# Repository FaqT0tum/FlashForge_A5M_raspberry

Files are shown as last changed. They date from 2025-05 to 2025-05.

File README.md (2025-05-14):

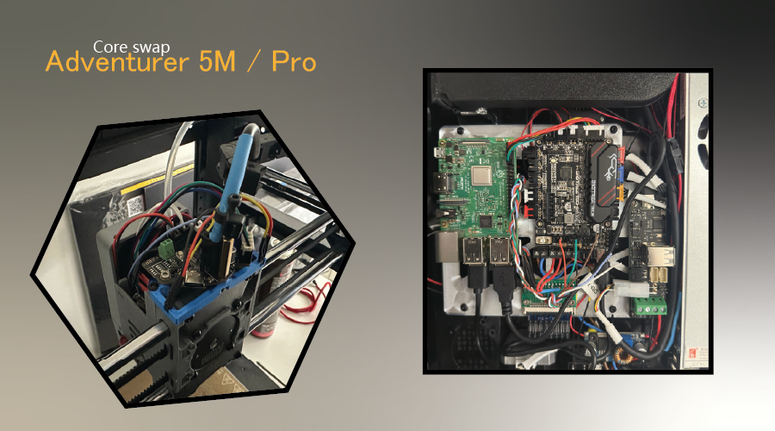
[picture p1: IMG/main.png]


The project will aim to completely replace all the electronics, leaving the original PSU, BED and head components.
 
 Some components will be mandatory and others can be replaced with what you prefer based on your needs.

## Components:

-  [FPC Brackout 30p 1mm](https://s.click.aliexpress.com/e/_oCeUnud) Bed wiring
-  [FPC Brackout 40p 0.5mm](https://s.click.aliexpress.com/e/_oB8gCY1) LCD Wiring (Coming soon)
-  [Hall effect A3144E](https://s.click.aliexpress.com/e/_oCG6PCH) Endstop X/Y
-  [Biqu EBB36 without MAX31865 v1.2](https://s.click.aliexpress.com/e/_oo8DyPB) Head Board
-  [Biqu U2C v2.1](https://s.click.aliexpress.com/e/_oo8DyPB) CAN transceiver
-  [Biqu SKR Pico v1](https://s.click.aliexpress.com/e/_omrGoLB) Main MCU
-  [Raspberry Pi Model B (at lest 1Gb)](https://s.click.aliexpress.com/e/_olvGKEN) SBC CPU Core
-  [Micro SD 64gb v30](https://s.click.aliexpress.com/e/_ooCZ32p) OS Memory (32gb v30 is also fine)
-  [Self-tapping M2.6 14mm](https://s.click.aliexpress.com/e/_oBh7XHr) Fixing screws
-  [Micro Molex 2x2](https://s.click.aliexpress.com/e/_olB1evL) to adapt EBB36
-  [Cable 22awg](https://s.click.aliexpress.com/e/_oD4gPCd) any extensions
-  [JST Crimping tool](https://s.click.aliexpress.com/e/_op3xPZP)
-  PETG 50g for adapters board

## Softwares
- [Raspberry PI Imager](https://www.raspberrypi.com/software/) Make File system
- [STM32 CubeProg](https://www.st.com/en/development-tools/stm32cubeprog.html) Flashing U2C/EBB36
- [Bitvise](https://bitvise.com/download-area) SSH for communicate with the Raspberry

## Configuration

- [Install Klipper (Kiauh)](https://github.com/dw-0/kiauh)
- [CanBus](https://github.com/FaqT0tum/FlashForge_A5M_raspberry/blob/main/CanBus/canbus.md)

## Electronics

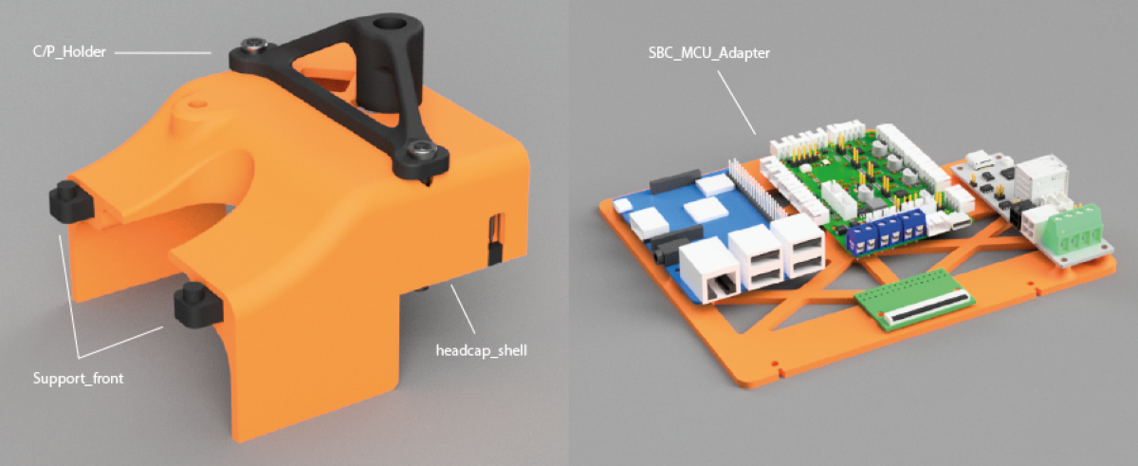
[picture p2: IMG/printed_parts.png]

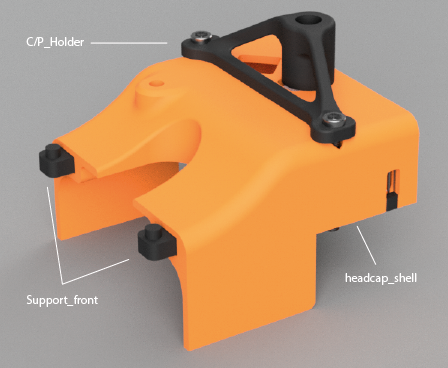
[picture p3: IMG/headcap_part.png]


<details>
<summary>Fan blower</summary>

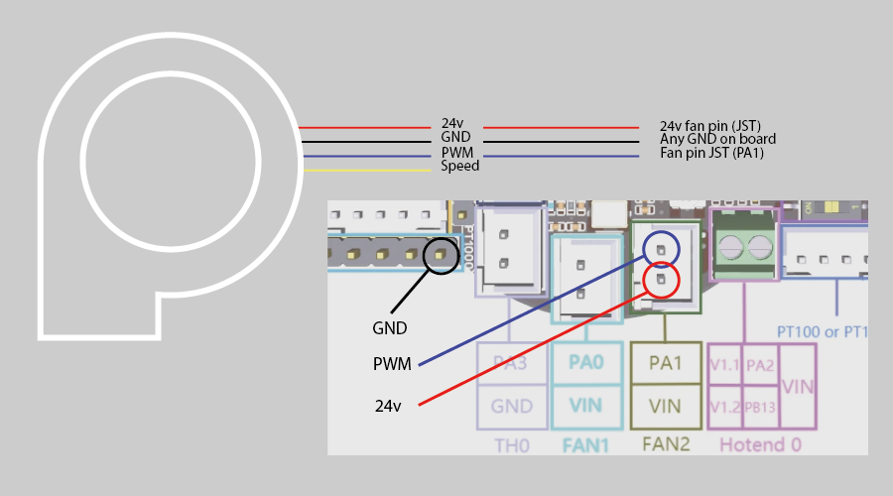
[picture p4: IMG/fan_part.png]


### Note: for the remaining FANS, the poles in the JST connectors must be reversed to adapt them to the SKR Pico

</details>

<details>
<summary>Filament runout</summary>

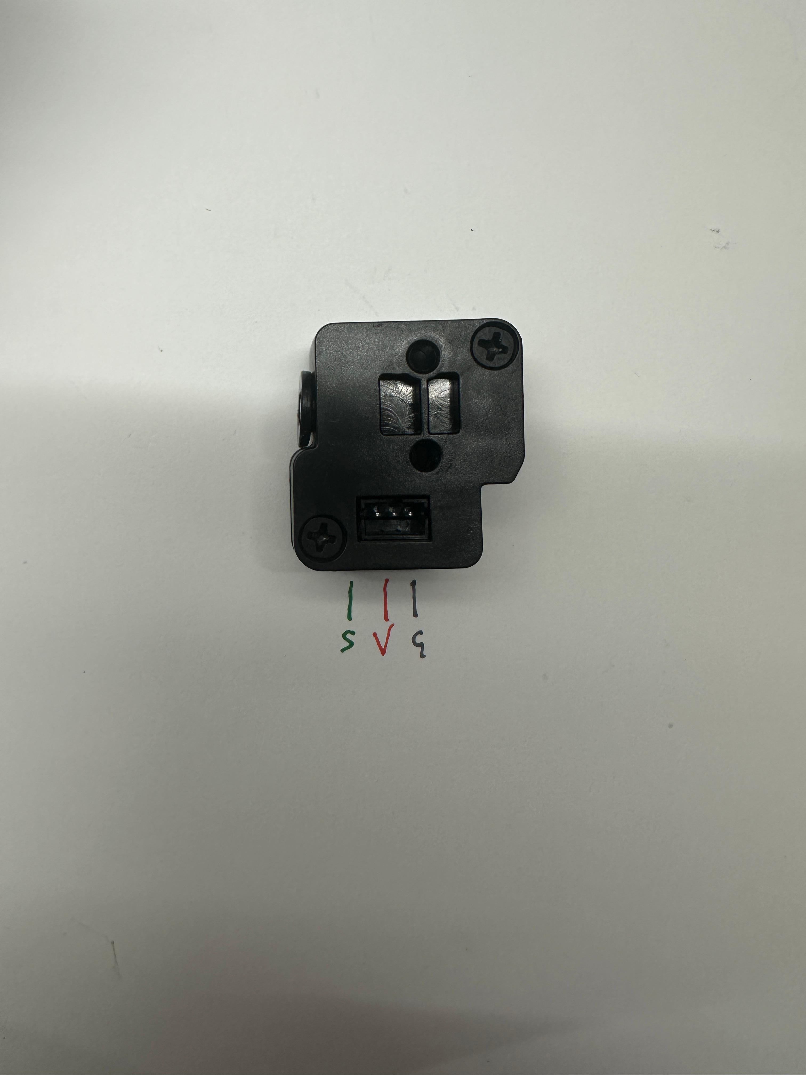
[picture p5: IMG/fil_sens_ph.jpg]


| Runout  | MCU |  
|:---:| :---:  |
| S | Signal | 
| V | 5V | 
| G | Ground | 

### Example

```bash
    [filament_switch_sensor runout_sensor]
    pause_on_runout: False
    switch_pin: !gpio3
    event_delay: 1.0
    runout_gcode:
        _FILAMENT_RUNOUT_EVENT
```

</details>

<details>
<summary>Heat Bed / Load Cell</summary>

### Connection diagram to reuse the original FFC and adapt it to the new MCU with a FPC Breakout 30p (1mm)

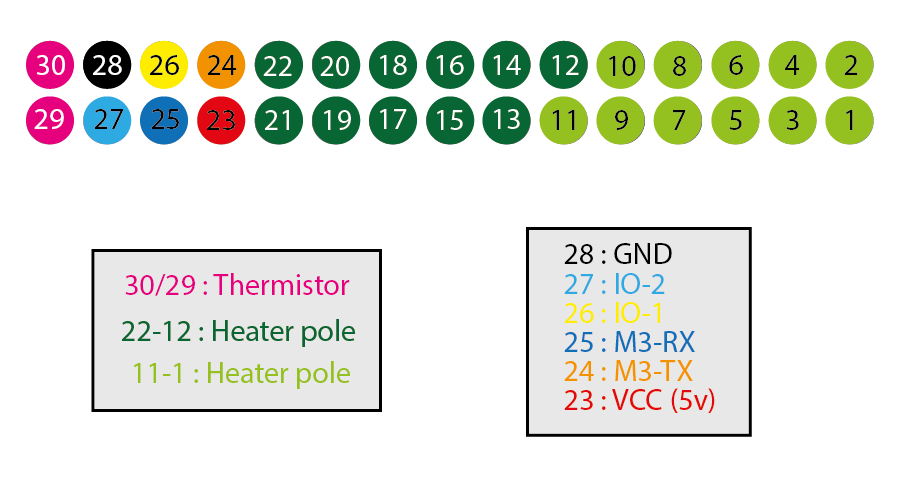
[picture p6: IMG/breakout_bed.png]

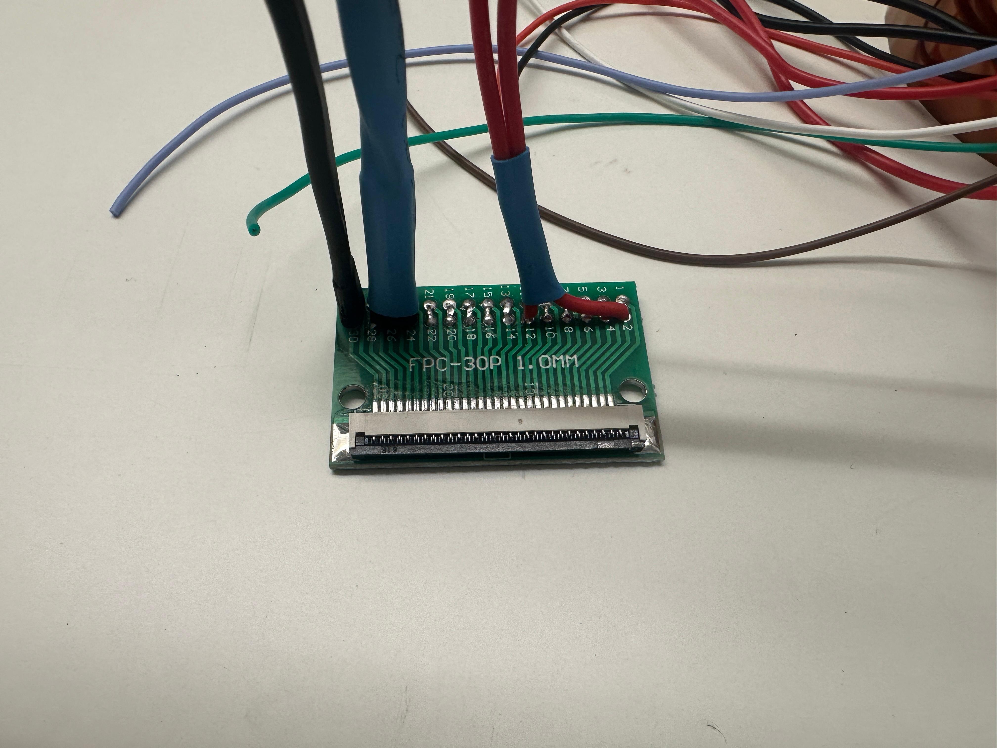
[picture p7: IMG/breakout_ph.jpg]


### Pins 23 to 28 are used for Load cell

### UPDATE: I was able to use the load cell system as a probe but without all the cell auto-calibration system without rebooting the board.
very simply, just connect the cables like this:

| FPC  | MCU |  
|:---:| :---:  |
| GND | GND | 
| VCC | 5V | 
| IO-1 | endstop pin | 

In my setup I connected everything to the JST x-stop of the SKR Pico using the reverse gpio4 pin (!)

```bash
    [probe]
    pin: !gpio4
    z_offset: -0.25
    speed: 2
    lift_speed: 5
    samples: 1
```

in the diagram below are shown the flashforge elettronics between Load_cell board --> FPC --> Main board. 
For future developments

| STC8G  | FPC | N32G455 | 
|:---:| :---:  | :---: |
| 1 | IO-2 | PB3 | 
| 3 | IO-1 | PB4 |  
| 5 | M3-TX  | PC12  | 
| 6 | M3-RX  | PD2 |  

</details>

<details>
<summary>Headtool board</summary>

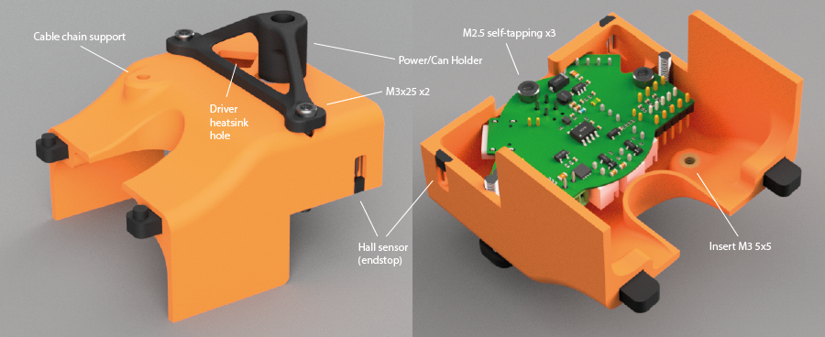
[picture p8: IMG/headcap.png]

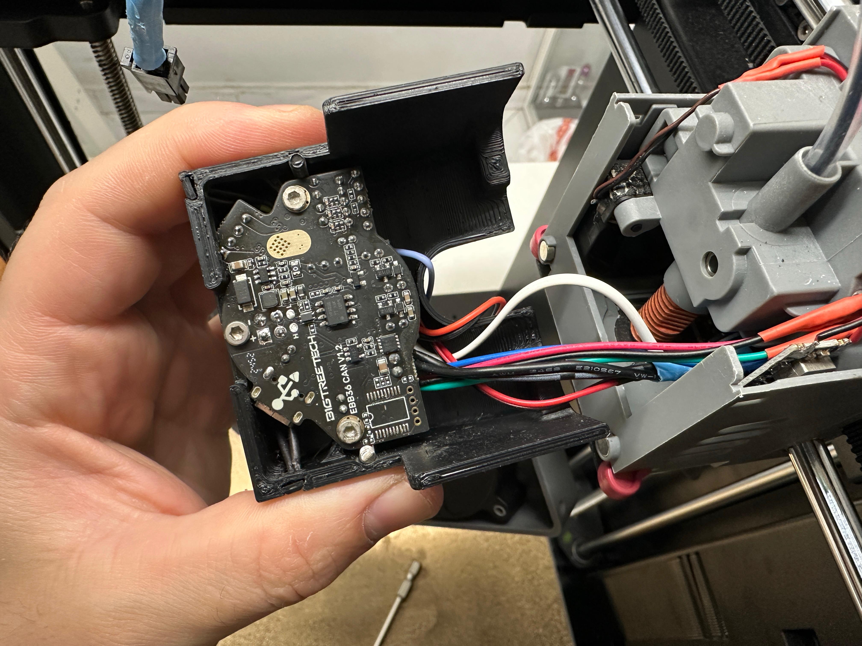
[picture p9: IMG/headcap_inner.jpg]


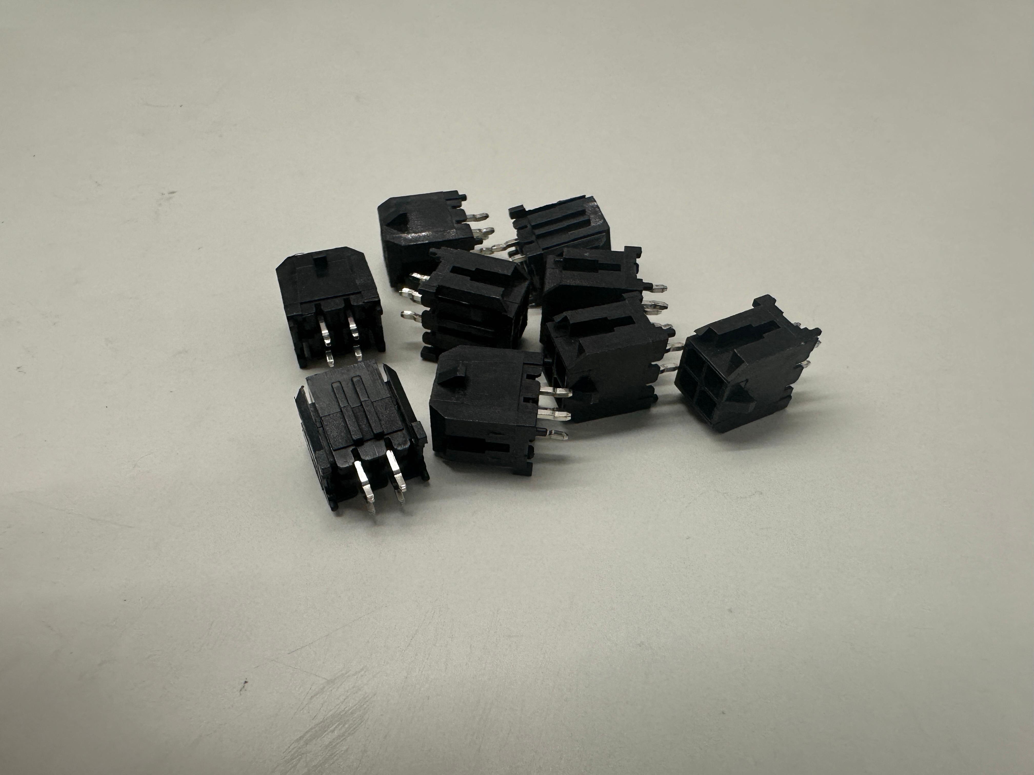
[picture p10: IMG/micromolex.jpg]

### For the assembly of the Had board requires a modification to the original Micro molex 2x2 90deg connector of the ebb36 with a straight one, Otherwise it will hit the back of the printer
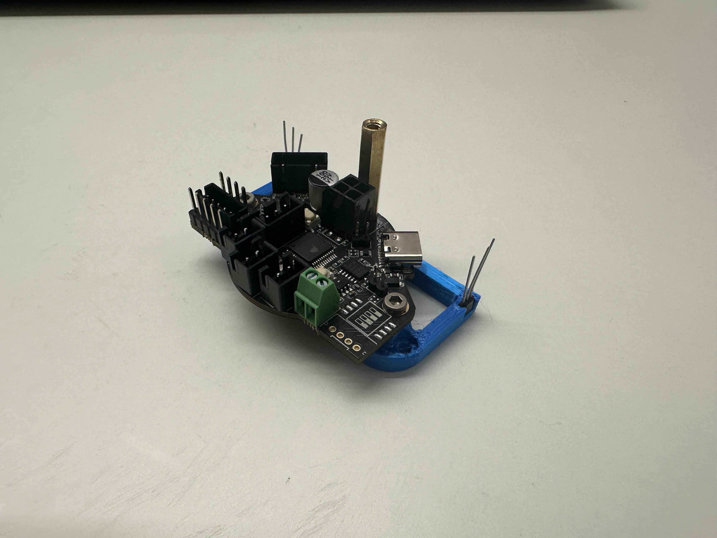
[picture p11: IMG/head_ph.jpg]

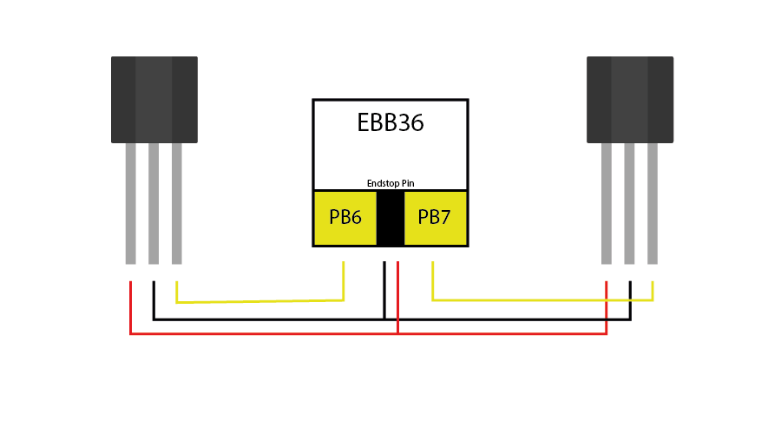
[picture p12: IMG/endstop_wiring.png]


</details>

### the above entries are expandable, click on the arrows

# Social

- [Instagram](https://www.instagram.com/faq_t0tum/)
- [YouTube](https://www.youtube.com/channel/UCHJ_528ZI0BcSU-QA8kIJlg)
- [PrusaPrinter](https://www.prusaprinters.org/social/218145-faqtotum/about)

# Buy me a coffee

This project is Free so if you have the pleasure of supporting my next works I will be grateful fot the coffee.  
[PayPal](https://www.paypal.me/MattiaRusso308?locale.x=it_IT)

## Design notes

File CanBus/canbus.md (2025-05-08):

# Configuration and installation of the Canbus U2C and EBB36 boards
The guide is based on Erik Zimmerman's, not because it is wrong, but to optimize it based on my experience and to minimize the problems I encountered.
The original guide can be found [here](https://github.com/EricZimmerman/VoronTools/blob/main/EBB_CAN.md) 

The components I used in this guide are:

1. Raspbery Pi 5
2. BTT U2C Version (2.1)
3. BTT EBB36 Version (1.2)
4. Some wire in the 22awg range
5. USB cables (I recommend that you make sure that the Type-C cable is not only power but also DATA)
6. A little patience :)

Before proceeding with the configuration of the various components, 
I recommend doing everything outside of the printer to make the various steps that will come easier for you.

# Raspberry setup

First we need to access the raspberry from the PC via SSH, to do this we will use Bitvise, entering the IP address that was assigned to the raspberry by the Router, in port we enter (22), username and password chosen during the creation of Raspberry OS.
If no user or password has been chosen you can use the default ones of the raspberry (User: pi / Password: raspberry). It is recommended to change at least the password at the first boot

1. Use mkdir to create a new folder with the command `sudo mkdir /etc/network/interfaces.d`
2. Use nano to create a new file with the command `sudo nano /etc/network/interfaces.d/can0`
3. Add the following code
    ```bash
    allow-hotplug can0
    iface can0 can static
     bitrate 1000000
     up ifconfig $IFACE txqueuelen 1024
     pre-up ip link set can0 type can bitrate 1000000
     pre-up ip link set can0 txqueuelen 1024
     ```

4. Use nano to create a new file with the command `sudo nano /etc/systemd/network/10-can.link`
5. Add the following code then save and exit nano
    ```bash
    [Match]
    Type=can
    
    [Link]
    TransmitQueueLength=1024
    ```

6. Use nano to create a new file with the command `sudo nano /etc/systemd/network/25-can.network`
7. Add the following code then save and exit nano
    ```bash
    [Match]
    Name=can*
    
    [CAN]
    BitRate=1M
    ```

8. Now you need to add a line to bottom in crontab for enable canbus at startup, with the command `sudo crontab -e`
9. Add the following code then save and exit nano. If asked for the editor type, select (1 - nano)
    ```bash

    @reboot sudo ip link set up can0 type can bitrate 1000000 &

    ```
10. Reboot the pi with `sudo reboot`

# U2C Flashing

Now to make sure that U2C has the right firmware we need to flash it with the correct version available [here](https://github.com/FaqT0tum/FlashForge_A5M_raspberry/blob/main/CanBus/G0B1_U2C_V2.zip)

1. The steps to flash this firmware are (taken from above link):
    - Download the STM32 CubePROG [here](https://www.st.com/en/development-tools/stm32cubeprog.html) 
    - Unzip the firmware file, previously downloaded
    - Press and hold the boot button on the u2c and plug the usb cable on PC, then release the boot button.
    - Launch STM32 CubePROG
    - Press the blue button that says (UART) and change it to (USB), and connect
    - Press on the green download symbol on the left
    - Browse and select a G0B1_U2C_V2.bin
    - Press (Start Programming)
    - unplug and reconnect the U2C to the Raspberry
    - Success
3. ADD THE JUMPER for the 120 ohm resistor to the U2C and set the U2C aside
    
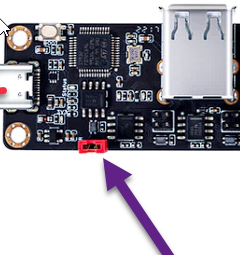
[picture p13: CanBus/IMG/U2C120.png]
    

# EBB36 Flashing

### Building Katapult (formerly known as CanBoot)

1. Clone the Katapult repository to your pi
    ```bash
    cd ~
    git clone https://github.com/Arksine/katapult
    ```

2. Run the following commands to bring up the menu to configure the firmware
    ```bash
    cd katapult
    make menuconfig
    ```
    
3. Starting from the top, make your firmware selections look exactly like the image below
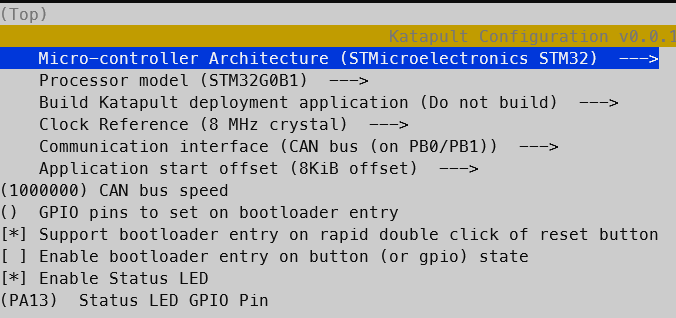
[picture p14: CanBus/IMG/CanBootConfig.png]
    

    NOTE: For Status LED GPIO Pin, be sure to enter **PA13**
    
4. Exit using `ESC` or `Q`, then confirm with yes (`Y`)
5. Build the firmware using the following commands:
    ```
    make clean
    make
    ```
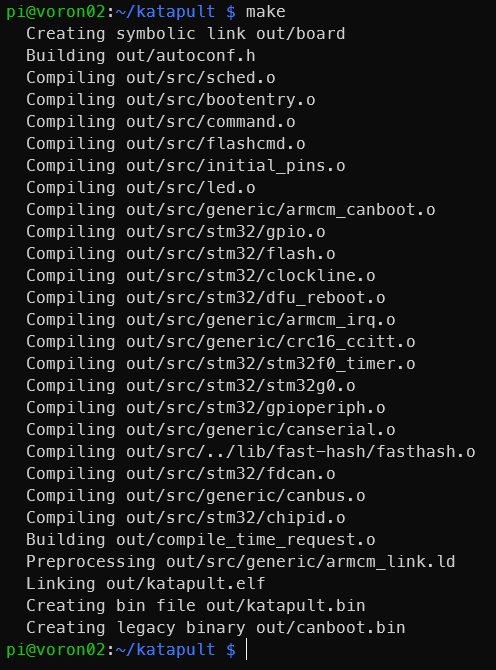
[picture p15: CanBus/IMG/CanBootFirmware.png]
    

### Flashing Katapult

1. Add a jumper as shown in the image below so the board can be powered via a USB connection
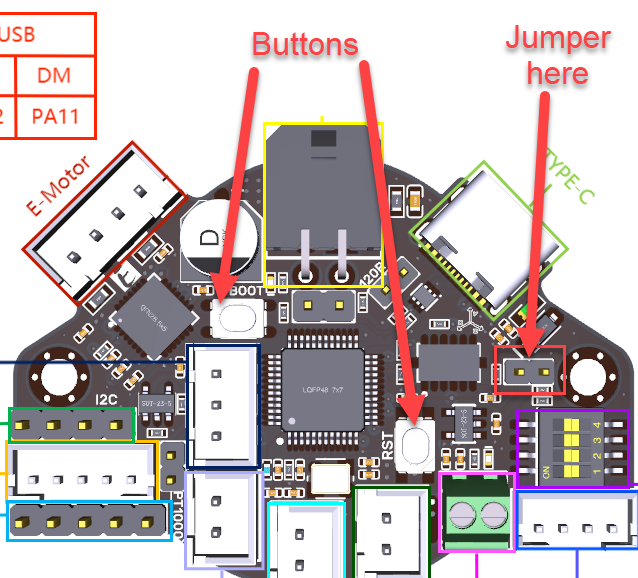
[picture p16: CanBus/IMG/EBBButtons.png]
    

2. Connect your device to your Pi via USB
3. Press and hold the `RESET` and `BOOT` buttons down (button locations shown in step 1)
    1. Release `RESET` button
    2. Release `BOOT` button
4. The device should now be in DFU mode. Verify this via the `lsusb` command, which should look something like this:
    ```
    Bus 001 Device 005: ID 0483:df11 STMicroelectronics STM Device in DFU Mode
    ```
5. Record the device ID (the part after `ID` above, but yours may be different)
6. Run the following command to erase and flash the EBB with Katapult (again, VERIFY your device ID. The ID is at the end of the command below):
    ```
    sudo dfu-util -a 0 -D ~/katapult/out/katapult.bin --dfuse-address 0x08000000:force:mass-erase:leave -d 0483:df11
    ```
7. The board will now be flashed. It will look similar to what is shown below. NOTE: If you see any mention of an error after the `File downloaded successfully` message, it can be ignored.

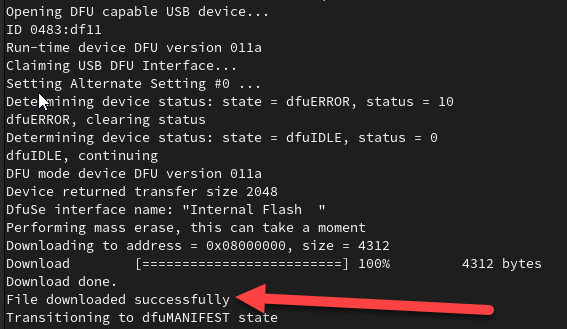
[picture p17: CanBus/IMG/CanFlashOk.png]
    
    
8. Unplug the board from USB and remove the USB jumper you installed for step 1
9. ADD THE JUMPER for the 120 ohm resistor to the EBB

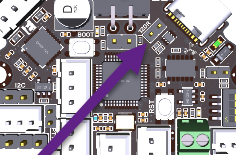
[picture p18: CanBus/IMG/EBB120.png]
    

### Verifying you see Katapult and flashing Klipper to the EBB

At this point, after checking twice that everything is connected correctly, power up the printer and SSH into the Pi.

1. Change directories into the klipper directory via `cd ~/klipper`
2. type `make menuconfig` and adjust things so it looks like the screenshot below

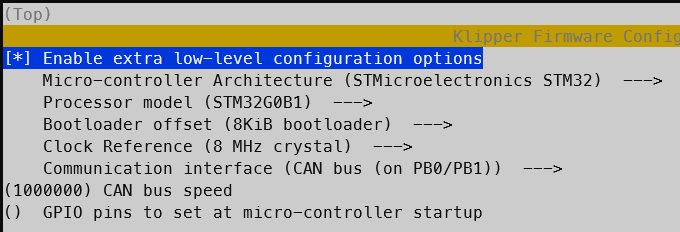
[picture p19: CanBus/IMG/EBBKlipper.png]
    

3. Exit, saving the changes, then build klipper by typing `make`
4. Find your UUID by running this command:
    ```bash
    sudo service klipper stop
    python3 ~/katapult/scripts/flashtool.py -i can0 -q
    ```
5. It should return something like:

    ```
    "Detected UUID: XXXXXXXXXX, Application: Katapult"
    ```

6. Record the UUID. This is YOUR uuid and will be used for the next step and in your cfg files.
7. Now its time to flash klipper via CAN! Run the following command, substituting your uuid:

   ```bash
   python3 ~/katapult/scripts/flashtool.py -i can0 -u b6d9de35f24f -f ~/klipper/out/klipper.bin
   ```
8. The EBB will be flashed and you should see a message about success, etc. Request for uuids again via:

   ```bash
    python3 ~/katapult/scripts/flashtool.py -i can0 -q
   ```

   but now, notice how it shows **Klipper** for the application! Yay!

9. Restart klipper via

   ```bash
   sudo service klipper start
   ```

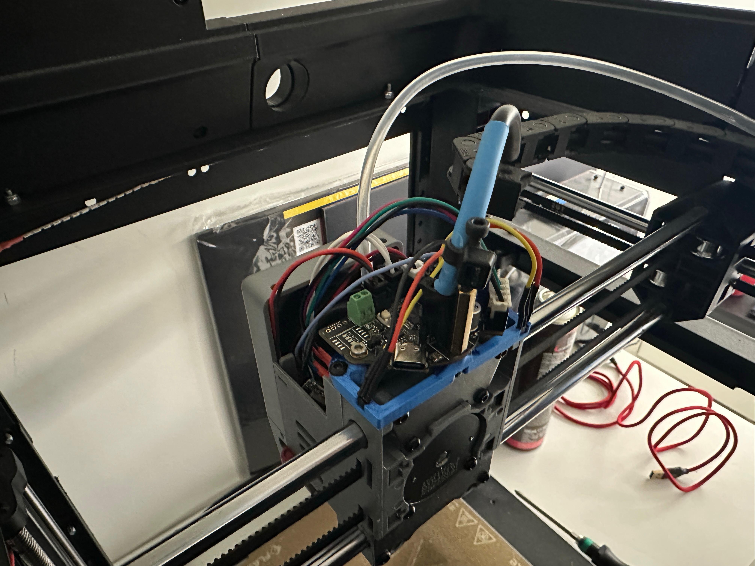
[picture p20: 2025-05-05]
IMG/head_pph.jpg

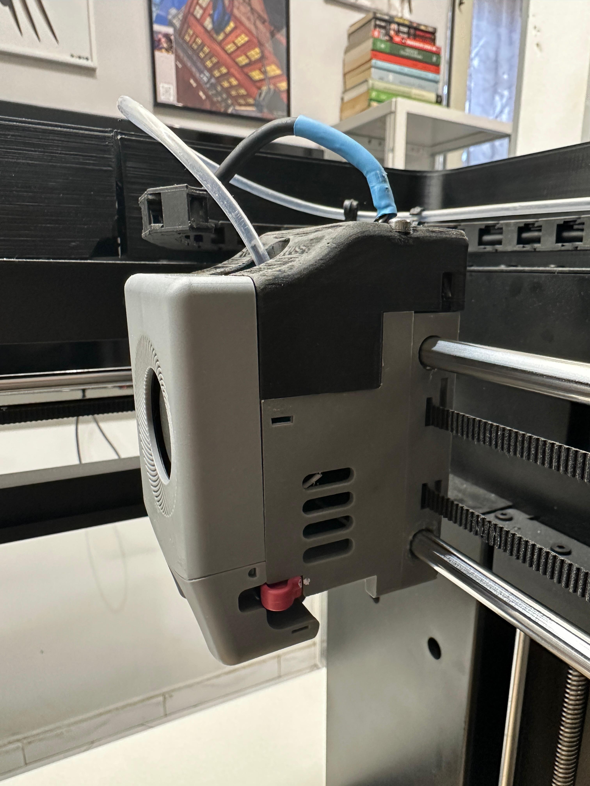
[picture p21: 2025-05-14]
IMG/headcap_side_ph.jpg

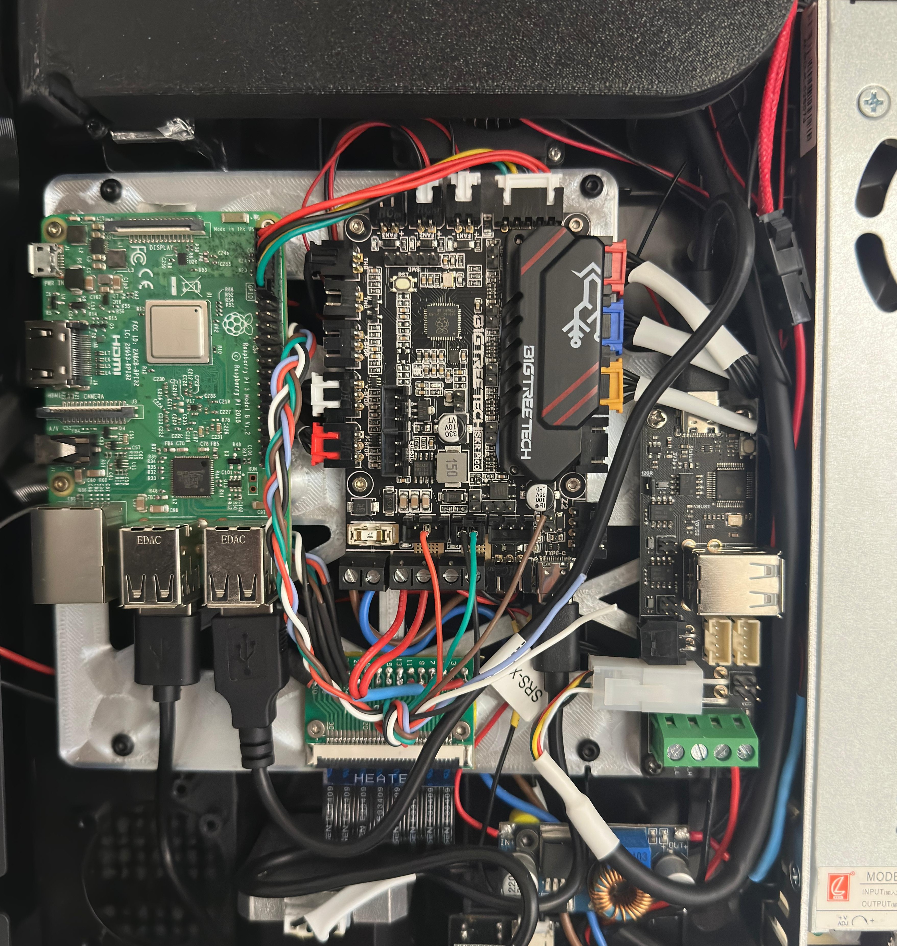
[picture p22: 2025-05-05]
IMG/main_ph.jpg

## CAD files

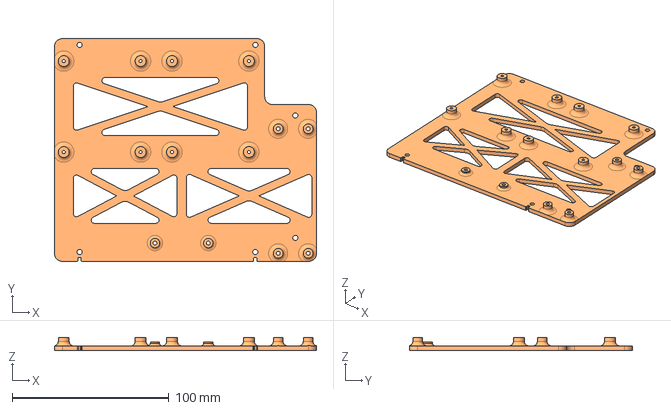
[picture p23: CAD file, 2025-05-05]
CAD/Main_board_adapt.step
167.0 x 142.0 x 8.50 mm

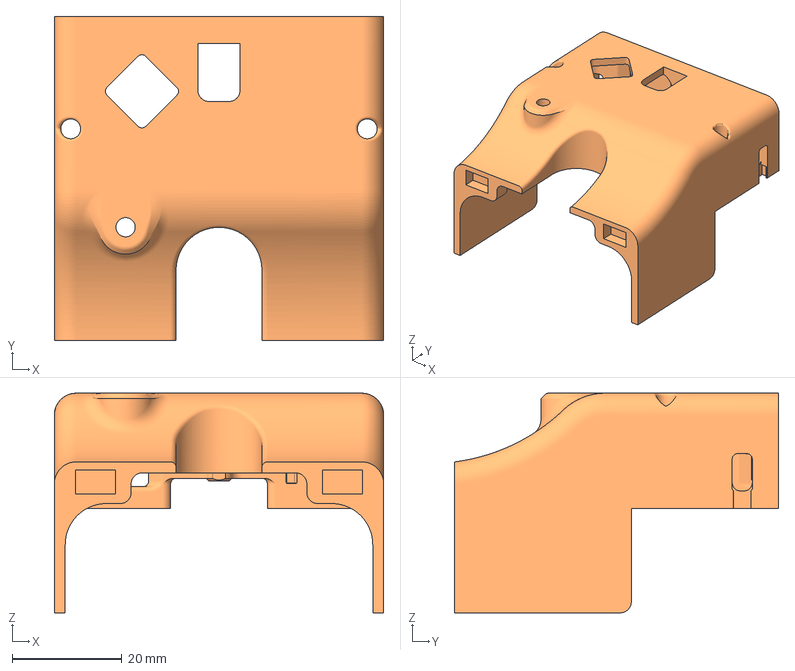
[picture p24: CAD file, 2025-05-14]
Printing File/Headcap/headcap_shell.3mf
60.0 x 59.0 x 40.0 mm

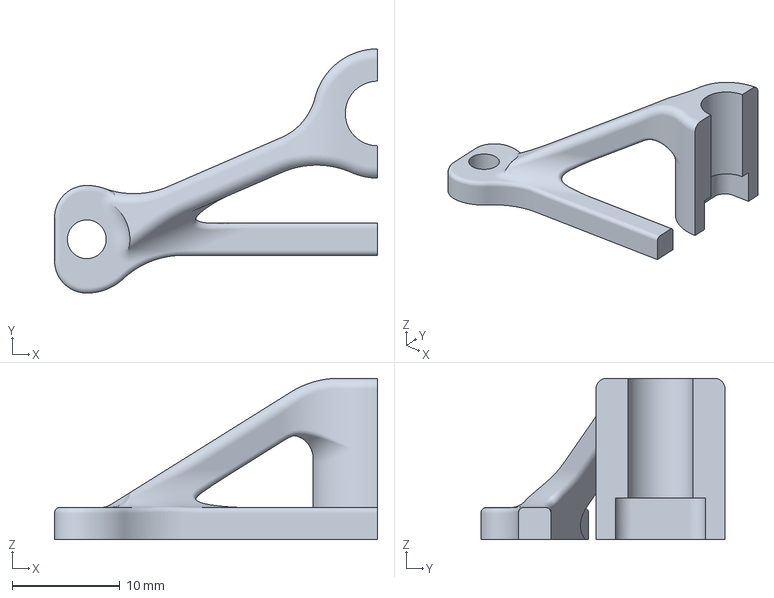
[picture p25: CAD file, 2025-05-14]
Printing File/Headcap/CP_holder_1.3mf
30.0 x 22.7 x 15.0 mm

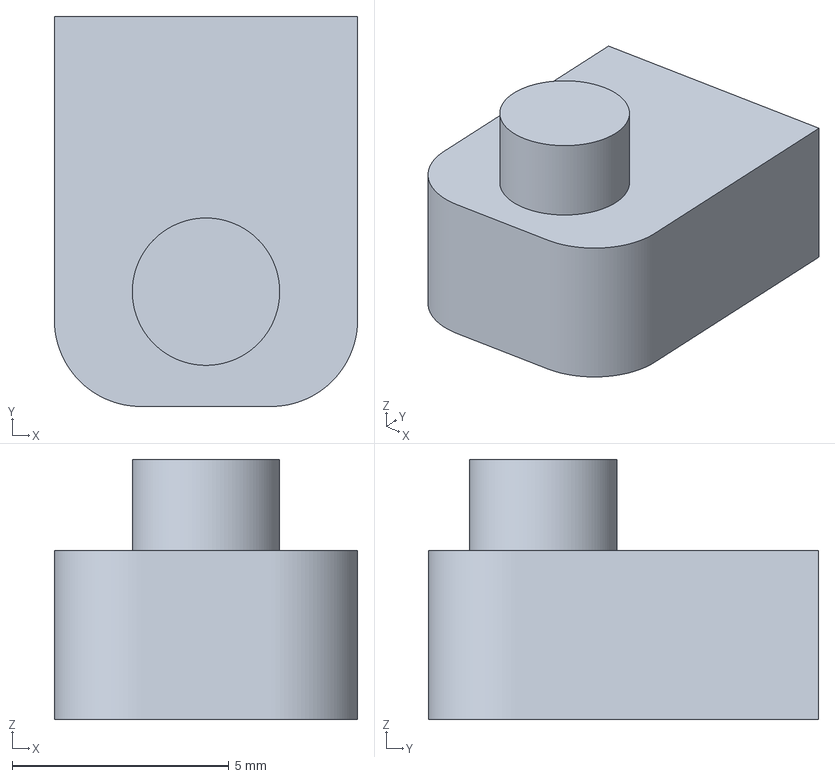
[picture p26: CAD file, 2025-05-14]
Printing File/Headcap/support_front_x2.3mf
7.00 x 9.00 x 6.00 mm

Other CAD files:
Printing File/SBC_MCU_adapter.3mf
Printing File/Headcap/CP_Holder_2.3mf

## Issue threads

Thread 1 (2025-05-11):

Alternative Extruder Boards?

ChaoticWeaponry, 2025-05-11:
Hi FaqT0tum!

I've been looking into alternative extruder boards to hopefully make it easier to create adapters and covers for the top.

I found 'Fly SB2040 v3' that has a similar shape to the stock extruder board, is there any reason why this wouldn't work?

FaqT0tum, 2025-05-11:
I checked a little while ago the feasibility of using the SB2040 and it seems like a great idea. I used the EBB because I already had it at home for another project.
the configuration procedure is almost the same as the EBB36, you can also use the U2C for the SB2040 in this case. you will only have to vary the creation of the katapult firmware by inserting the appropriate information such as the type of MCU which in this case is an RP2040 and not STM32 as for the EBB36 and the CAN pins.
If I can I will take it too, so as to bring an alternative into the project

FaqT0tum, 2025-05-12:
I downloaded the CAD file of the SB2040 to see if it could fit well, but I noticed that the JST for connection to the extruder and positioned below, would mean raising the board too much. There is no space in the head to exploit in that position

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

FaqT0tum, 2025-05-12:
This is what I have drawn for now, it still needs to be fixed and then I will proceed with the tests

For EBB36

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

ChaoticWeaponry, 2025-05-12:
> I downloaded the CAD file of the SB2040 to see if it could fit well, but I noticed that the JST for connection to the extruder and positioned below, would mean raising the board too much. There is no space in the head to exploit in that position
>
> 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

I think it could be manageable if it was re-soldered to the top of the board, I'm experimenting with designs in Blender to see if it could be possible.

ChaoticWeaponry, 2025-05-12:
Nevermind. It looks like the through-holes on the circuit board are offset for the XT30 connector. Right angle is offset, straight is inline. So you would not be able to replace the power/CAN connector without serious modification.. Bummer

FaqT0tum, 2025-05-12:
Yes! Too bad, the form factor would have been perfect.

Domani stampo questo, dovrebbe essere pronto

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

ChaoticWeaponry, 2025-05-12:
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

You're a lot faster than I am. This looks fantastic.

Question, do the hall effect sensors have a 'range'? The OEM ones are covered by the plastic top (1-2mm thick) and still work correctly, I think we could hide the sensors to make it look even better.

FaqT0tum, 2025-05-12:
I mounted them like this and they worked the first time, but yes I did not check this to optimize. I take a look at them before printing and then if necessary I move them.

I just hope I don't go crazy assembling it because the board has to be inserted from underneath hahahahah

ChaoticWeaponry, 2025-05-12:
> I mounted them like this and they worked the first time, but yes I did not check this to optimize. I take a look at them before printing and then if necessary I move them.
>
> I just hope I don't go crazy assembling it because the board has to be inserted from underneath hahahahah

We can make revisions to make assembly easier.
The first couple versions are prototypes 😂

ChaoticWeaponry, 2025-05-13:
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

I'm definitely way behind you on 3D modeling skills, but this is the idea I had in my head.

The hall effect sensors are recessed ~1mm from the edges, and there's additional mount points for the top cover so you can assemble everything in steps. I don't think the bowden tube support is necessary, but I don't know if it could potentially contact the EBB36 board.

ChaoticWeaponry, 2025-05-13:
Sounds good. I'll be able to buy the parts starting next month (I've already exceeded my budget lol)

If you need fitment tested I have 3kg of PET-CF filament and a spare complete extruder assembly, I'd be happy to help out.

FaqT0tum, 2025-05-13:
I intended to design the entire headtool from scratch to include more performing extruders and hotends, reduce space and weight.

I was thinking of using the Bambulab hotend and the Creality K1 extender

ChaoticWeaponry, 2025-05-13:
Cool! I've been using a X1C hotend in my AD5M for a while now, haven't had any issues. Though everything else is still stock components (E-board, extruder, extruder motor, etc)

FaqT0tum, 2025-05-13:
### Everything went well the first time, the assembly was easy thanks to the long enough cables. I have to add now a support for the chain and for the CAN/Power cable.

Hall sensors can be moved on the Y-axis to put them inside but on the X-axis there is already too much distance. The sensor should be changed with a more performing one or a magnet added on the X-axis. I leave everything as it is, better to have margin

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

ChaoticWeaponry, 2025-05-13:
Looks great! Excited to see the potential of this printer with better hardware.

FaqT0tum, 2025-05-14:
I have uploaded everything, both the print and CAD files

ChaoticWeaponry, 2025-05-14:
> I have uploaded everything, both the print and CAD files

Awesome! I’ll take a look when I get off work.

Do you mind if I use the CAD files and modify them?

ChaoticWeaponry, 2025-05-15:
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

So.... against my better judgement, I want to see if I can make something that will work with the SB2040 v3. It's going to require A LOT of modification to the board. I just think the shape of it works too well.

So far the power and CAN connections will have to be separate connectors, power connector will need to be straight, hotend heater connector will need to be swapped to the other side of the board, and the extruder motor connector will need to be relocated.

FaqT0tum, 2025-05-15:
I don't know how feasible it is to make all these changes on a Chinese card of modest quality. From experience the less you touch them the better.
Good luck 😊

ChaoticWeaponry, 2025-05-18:
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

This is the progress so far modeling the extruder body and cap. I'll likely have to create some kind of strain relief for the power connection.

FaqT0tum, 2025-05-18:
wow, congratulations. update me especially when you have to modify the board. I'm very curious

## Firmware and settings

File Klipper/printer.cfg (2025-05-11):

#[include file.cfg]
[include macros.cfg]
[include mainsail.cfg]

[mcu head]
canbus_uuid: 171a30843a8b

[mcu]
serial: /dev/serial/by-id/usb-Klipper_rp2040_454741505A88F85A-if00
restart_method: command

[temperature_sensor RPi]
sensor_type: temperature_host

[printer]
kinematics: corexy
max_velocity: 600
max_accel: 20000
max_z_velocity: 25
max_z_accel: 500
square_corner_velocity: 25


[stepper_x]
step_pin: gpio14
dir_pin: gpio13
enable_pin: !gpio15
microsteps: 16
rotation_distance: 40
endstop_pin: !head:PB6
position_endstop: 220
position_max: 220.1
position_min: 0
homing_speed: 50
homing_retract_dist: 5
homing_retract_speed: 25
second_homing_speed: 5

[stepper_y]
step_pin: gpio11
dir_pin: gpio10
enable_pin: !gpio12
microsteps: 16
rotation_distance: 40
endstop_pin: !head:PB7
position_endstop: 220
position_max: 220.1
position_min: 0
homing_speed: 50
homing_retract_dist: 5
homing_retract_speed: 25
second_homing_speed: 5


[stepper_z]
step_pin: gpio6
dir_pin: gpio5
enable_pin: !gpio7
microsteps: 16
rotation_distance: 8
endstop_pin: ^gpio25
position_endstop: 220
position_max: 230
position_min: -10
homing_speed:25
homing_retract_dist: 5
homing_retract_speed: 12.5
second_homing_speed: 5

[extruder]
step_pin: head:PD0
dir_pin: !head:PD1
enable_pin: !head:PD2
microsteps: 16
rotation_distance: 4.4
nozzle_diameter: 0.400
filament_diameter: 1.750
heater_pin: head:PB13
sensor_type: Generic 3950
sensor_pin: head:PA3
control = pid
pid_kp = 33.443
pid_ki = 4.372
pid_kd = 63.961
min_temp: -100
max_temp: 350
pressure_advance:0.035
pressure_advance_smooth_time: 0.040
max_extrude_only_distance:1500.00
max_extrude_cross_section:1000

[tmc2209 stepper_x]
uart_pin: gpio9
tx_pin: gpio8
uart_address: 3
interpolate:True
run_current: 0.9
#hold_current:0.3
#sense_resistor:0.10
#stealthchop_threshold: 999999

[tmc2209 stepper_y]
uart_pin: gpio9
tx_pin: gpio8
uart_address: 0
interpolate:True
run_current: 0.9
#hold_current:0.3
#sense_resistor:0.10
#stealthchop_threshold: 999999

[tmc2209 stepper_z]
uart_pin: gpio9
uart_pin: gpio9
tx_pin: gpio8
uart_address: 2
interpolate:True
run_current: 0.9
hold_current:0.6
#sense_resistor:0.10
#stealthchop_threshold: 999999

[tmc2209 extruder]
uart_pin: head:PA15
interpolate:True
run_current: 0.8
hold_current:0.8
#sense_resistor:0.10
#stealthchop_threshold: 999999

[heater_bed]
heater_pin: gpio21
sensor_type: Generic 3950
sensor_pin: gpio26
#pullup_resistor: 4700
control = pid
pid_kp = 74.793
pid_ki = 1.619
pid_kd = 863.863
#max_power: 1.0
min_temp: -100
max_temp: 130

[verify_heater extruder]
max_error: 290
check_gain_time:200
hysteresis: 10
heating_gain: 10

[verify_heater heater_bed]
max_error: 120
check_gain_time:200
hysteresis: 10
heating_gain: 10

[led chamber_led]                                                   
white_pin: gpio23                                                 
hardware_pwm: False
initial_white: 1

[heater_fan hotend_fan]
pin: head:PA0
max_power: 1.0
#kick_start_time: 0.5
heater: extruder
heater_temp: 50.0

[fan]
pin: head:PA1
max_power: 0.6
cycle_time:  0.00004
hardware_pwm: False 
kick_start_time: 0.100
enable_pin: head:PB4

[controller_fan stepper_driver_fan]
pin:gpio17
stepper: stepper_x, stepper_y, stepper_z
fan_speed: 0.6
idle_timeout: 0

[filament_switch_sensor runout_sensor]
pause_on_runout: False
switch_pin: !gpio3
event_delay: 1.0
runout_gcode:
    _FILAMENT_RUNOUT_EVENT

[input_shaper]
shaper_type_x = mzv
shaper_freq_x = 64.2
shaper_type_y = mzv
shaper_freq_y = 51.4

[adxl345]
cs_pin: head:PB12
spi_speed: 1000000
#spi_bus: spi3
spi_software_sclk_pin: head:PB10
spi_software_mosi_pin: head:PB11
spi_software_miso_pin: head:PB2
axes_map:  x, y, z
rate: 800

[resonance_tester]
accel_chip:adxl345
min_freq: 5
max_freq: 100
probe_points:
        110,110,110

[idle_timeout]
timeout:600

[pause_resume]
recover_velocity: 50

[gcode_arcs]
resolution: 1.0

[exclude_object]

[homing_override]
gcode:
    M204 S5000
    G28 Z0
    G28 X0
    G28 Y0
    G90
    G1 X105 Y105 Z210 F9000

                
[bed_mesh]                         
speed: 300                          
horizontal_move_z:1
move_check_distance: 5
mesh_min: 0, 25          
mesh_max: 220, 220             
probe_count: 9, 9                  
mesh_pps: 3, 3                     
algorithm: bicubic                 
bicubic_tension: 0.2               
#fade_start: 3
#fade_end: 10
#fade_target: 0
                                  
[probe]
pin: !gpio4
speed: 2
lift_speed: 5
samples: 2

#*# <---------------------- SAVE_CONFIG ---------------------->
#*# DO NOT EDIT THIS BLOCK OR BELOW. The contents are auto-generated.
#*#
#*# [probe]
#*# z_offset = -0.315
#*#
#*# [bed_mesh default]
#*# version = 1
#*# points =
#*# 	  -0.226250, -0.255000, -0.241250, -0.286250, -0.298750, -0.267500, -0.255000, -0.261250, -0.295000
#*# 	  -0.271250, -0.282500, -0.293750, -0.296250, -0.340000, -0.317500, -0.293750, -0.322500, -0.381250
#*# 	  -0.297500, -0.291250, -0.325000, -0.322500, -0.356250, -0.365000, -0.348750, -0.348750, -0.445000
#*# 	  -0.302500, -0.305000, -0.326250, -0.342500, -0.367500, -0.373750, -0.357500, -0.401250, -0.448750
#*# 	  -0.311250, -0.315000, -0.311250, -0.315000, -0.368750, -0.355000, -0.368750, -0.362500, -0.473750
#*# 	  -0.313750, -0.276250, -0.281250, -0.322500, -0.350000, -0.351250, -0.335000, -0.352500, -0.408750
#*# 	  -0.276250, -0.252500, -0.247500, -0.273750, -0.290000, -0.283750, -0.272500, -0.291250, -0.380000
#*# 	  -0.275000, -0.222500, -0.248750, -0.232500, -0.235000, -0.248750, -0.245000, -0.226250, -0.302500
#*# 	  -0.215000, -0.180000, -0.156250, -0.180000, -0.196250, -0.178750, -0.150000, -0.156250, -0.237500
#*# x_count = 9
#*# y_count = 9
#*# mesh_x_pps = 3
#*# mesh_y_pps = 3
#*# algo = bicubic
#*# tension = 0.2
#*# min_x = 0.0
#*# max_x = 220.0
#*# min_y = 25.0
#*# max_y = 219.96000000000004

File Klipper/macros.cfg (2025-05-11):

# define overrides for Mainsail/Fluidd predefined macros - see client.cfg
[gcode_macro _CLIENT_VARIABLE]
variable_use_custom_pos   : True ; use custom park coordinates for x,y [True/False]
variable_custom_park_x    : 110.0  ; custom x position; value must be within your defined min and max of X
variable_custom_park_y    : 220.0  ; custom y position; value must be within your defined min and max of Y
variable_custom_park_dz   : 10.0    ; custom dz value; the value in mm to lift the nozzle when move to park position
variable_speed_hop        : 25.0    ; z move speed in mm/s
variable_speed_move       : 300.0   ; move speed in mm/s
variable_park_at_cancel   : True    ; allow to move the toolhead to park while execute CANCEL_PRINT [True/False]
variable_park_at_cancel_x : 110     ; different park position during CANCEL_PRINT [None/Position as Float]; park_at_cancel must be True
variable_park_at_cancel_y : 220     ; different park position during CANCEL_PRINT [None/Position as Float]; park_at_cancel must be True
variable_runout_sensor    : "filament_switch_sensor runout_sensor"
gcode:

[gcode_macro START_PRINT]
gcode:
    {% set bed_temp = params.BED_TEMP|default(60)|float %}             ; bed temp, usually set by slicer
    {% set extruder_temp = params.EXTRUDER_TEMP|default(200)|float %}  ; extruder temp, usually set by slicer
    {% set disable_priming = params.DISABLE_PRIMING|default(false) %}  ; allow disabling of priming before print
    {% set disable_skew = params.DISABLE_SKEW_CORRECT|default(false) %}; if true it will not apply the skew correction profile
    {% set force_leveling = params.FORCE_LEVELING|default(false) %}    ; if true it forces the bed level process

    BED_MESH_PROFILE LOAD=default
    
    M140 S{bed_temp}        ; start bed heating
    SET_GCODE_OFFSET Z=0.0  ; reset the G-Code Z offset (adjust Z offset if needed)
    G28                     ; home the printer

  
    G90                     ; use absolute coordinates
    G1 Z10 F1800            ; move the nozzle near the bed
    # wait for bed to reach temp, don't wait for stabilization
    TEMPERATURE_WAIT SENSOR=heater_bed MINIMUM={bed_temp}
    M109 S{extruder_temp}   ; set and wait for nozzle to reach temperature


    G90
    M83
    G1 E-1.5 F800
    G1 X220 Y220 F6000
    G1 E2 F800
    G1 Y220 X55 Z0.25 F4800
    G1 X155 E8 F2400
    G1 Y219.6 F2400
    G1 X55 E5 F2400
    G1 Y220 X55 Z0.45 F4800
    G1 X155 E8 F2400
    G1 Y219.6 F2400
    G1 X55 E5 F2400
    G92 E0

[gcode_macro END_PRINT]
gcode:
    G91                     ; relative positioning
    G1 X-2 Y-2 E-5 F2000    ; move away while retracting filament
    M104 S0                 ; turn off extruder temperature
    M140 S0                 ; turn off bed temperature
    M107                    ; turn off part cooling fan
    G90                     ; absolute positioning
    G1 X110 Y110 Z220 F1500 ; move near end stop position
    M84                     ; disable motors
    
[gcode_macro AUTO_BED_LEVEL]
gcode:
    {% set bed_temp = params.BED_TEMP|default(60)|float %}
    {% set extruder_temp = params.EXTRUDER_TEMP|default(200)|float %}
    {% set profile = params.PROFILE|default("default") %}

    # clear old mesh and home if necessary
    BED_MESH_CLEAR
    {% if not "xyz" in printer.toolhead.homed_axes %}
        G28
    {% endif %}

    # bed heating
    G90                     ; absolute coordinates
    G1 Z10 F1800            ; raise bed
    M140 S{bed_temp}        ; set bed temp
    # wait for bed to reach temp, don't wait for stabilization
    TEMPERATURE_WAIT SENSOR=heater_bed MINIMUM={bed_temp}

    # nozzle heating
    M104 S{extruder_temp}   ; set nozzle temperature
    # wait for nozzle to reach temp, don't wait for stabilization
    TEMPERATURE_WAIT SENSOR=extruder MINIMUM={extruder_temp}

    # wipe to left
    G90                     ; absolute coordinates
    G1 X50 Y220 Z5 F18000   ; get into position
    PROBE                   ; moove nozzle to bed
    G91                     ; relative position
    G1 X40 F900            ; wipe move left

    # wipe to right
    G90                     ; absolute coordinates
    G1 X50 Y220 Z5 F18000  ; get into position
    PROBE                   ; moove nozzle to bed
    G91                     ; relative position
    G1 X40 F900             ; wipe move right


    # wait for nozzle cooldown to 120°
    M106 S255               ; turn on fan
    M104 S0                 ; turn of noozle heating
    TEMPERATURE_WAIT SENSOR=extruder MAXIMUM=120
    M107                    ; turn off fan


    # move to remove cold filament
    G1 X10 F300

    # start the calibration
    BED_MESH_CALIBRATE PROFILE={profile}

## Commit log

2025-05-11 ADD runout sensor
    [printer.cfg]
2025-05-11 Add end gcode
    [macros.cfg]
